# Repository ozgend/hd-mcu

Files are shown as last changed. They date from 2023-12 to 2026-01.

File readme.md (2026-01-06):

# hd-mcu

## bluetooth supported mcu for harley davidson 99-03 with raspberry pi pico

this is not a ecu but a diy -and for fun- project for a monitoring hardware via an mcu since there is no [can-bus](https://en.wikipedia.org/wiki/CAN_bus) support for 99-03 models. it replaces the default turn signal module (tsm) to provide monitoring features for battery voltage, rpm, voes, ignition, and external thermo sensors via bluetooth to the mobile application. it does not involve a reverse engineering for the original hd-tsm module.

- programmable idle timeout for turn signal
- pcb provides signal switching via h-bridge module or mosfet + oc
- built-in battery voltage sensor
- built-in rpm reader
- built-in temperature sensor via rpi-pico
- aux inputs for ignition and voes signals _(may require custom ignition module ie. [ultima/dyna 2000i](./doc/ud2000i.pdf))_
- vehicle information with editable fields for maintenance records
- external 6x thermocpouler raiser for max6670
- supports up to 8x thermocpouler sensors for various purposes

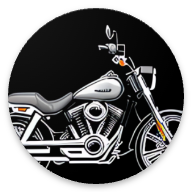
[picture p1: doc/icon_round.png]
icon


### features

- [x] hardware serial
  - [x] raw ft232 usb serial
- [x] bluetooth serial
  - [x] raw bluetooth serial (hc-06 @ 9600 bps)
  - [x] mobile app
- [x] data polling/broadcasting
  - [x] reduced power consumption
  - [x] reduced cpu clock usage
- [x] turn signal flasher module
  - [x] left/right turn signal flasher
  - [x] hazard flasher
  - [x] flash on startup
  - [x] adjustable flash rate
- [x] throttle control module
  - [x] linear hall sensor input
  - [x] servo pwm output
  - [x] adjustable base parameters
  - [x] adjustable idle speed
  - [ ]
  - [ ] adjustable throttle curves
- [x] supported sensor inputs
  - [x] multiplexed thermocouples
    - [x] up to 8 thermocouples
  - [x] direct sensor inputs
    - [x] uptime counter (onboard)
    - [x] mcu voltage (onboard)
    - [x] temperature (onboard)
    - [x] vbus input (onboard)
    - [x] battery voltage input
    - [x] rpm input
    - [x] speed input
  - [ ] tpms
    - [ ] 433mhz receiver implementation
    - [ ] tpms decoder / man-i or man-ii (tbd)
  - [ ] ignition module
    - [ ] dyna 2000i / ultima 2000i timer & pickup
    - [ ] programmable ignition advance
      - [ ] advance curve
      - [ ] temp compensation
      - [ ] rpm compensation
      - [ ] wideband o2 sensor for afr

### software

**mobile app**

- platform

  - `react 18.2.0`
  - `react-native: 0.73.2`

- react-native
  - [x] android
  - [ ] ios

### mobile app ui

back

**mcu firmware**

- platform

  - `nodejs: 20`
  - [`kaluma-cli: 1.4.0`](https://kalumajs.org/docs/getting-started)
  - [`kalumajs runtime: 1.2.1`](https://kalumajs.org/download/)

- FLASH: 2044/24 kb
- SRAM: 264 total, 184/62 kb

### hardware

**assembly**

- 12v-5v buck converter / switching regulator
  - [lm2596 datasheet](./doc/lm2596.pdf)
- raspberry pi pico
  - [pinout](https://pico.pinout.xyz/)
  - [datasheet](./doc/pico-datasheet.pdf)
- hc-06 bluetooth module
  - [datasheet](./doc/hc06.pdf)
- `TSM` / turn signal module
  - _(option-1)_ - with mosfet extension board
    - _pick this if your rectifier is 3 pin and charge flux is 12v-15v_
    - [IRF4905 datasheet](./doc/IRF4905.pdf)
  - _(option-2)_ - l298n h-bridge driver module
    - [datasheet](./doc/l298.pdf)
- `THE` / thermocouple module
  - cd4051 multiplexer
    - [datasheet](./doc/cd4051b.pdf)
  - max6675 thermocouple digitizer
    - [datasheet](./doc/MAX6675.pdf)
    - k-type thermocouple (maximum of 8)
- `TCM` / throttle control module
  - [linear hall sensor / 49e](./doc/49e.pdf)
  - [DS3230MG digital servo](./doc/ds3230.pdf)
- 5v super capacitor
- 5805 voltage regulator
- 33k resistor
- 10k resistor
- 7.5k resistor
- 4.7k resistor
- 1k resistor
- 1n4001 diode

### pcb

**front**
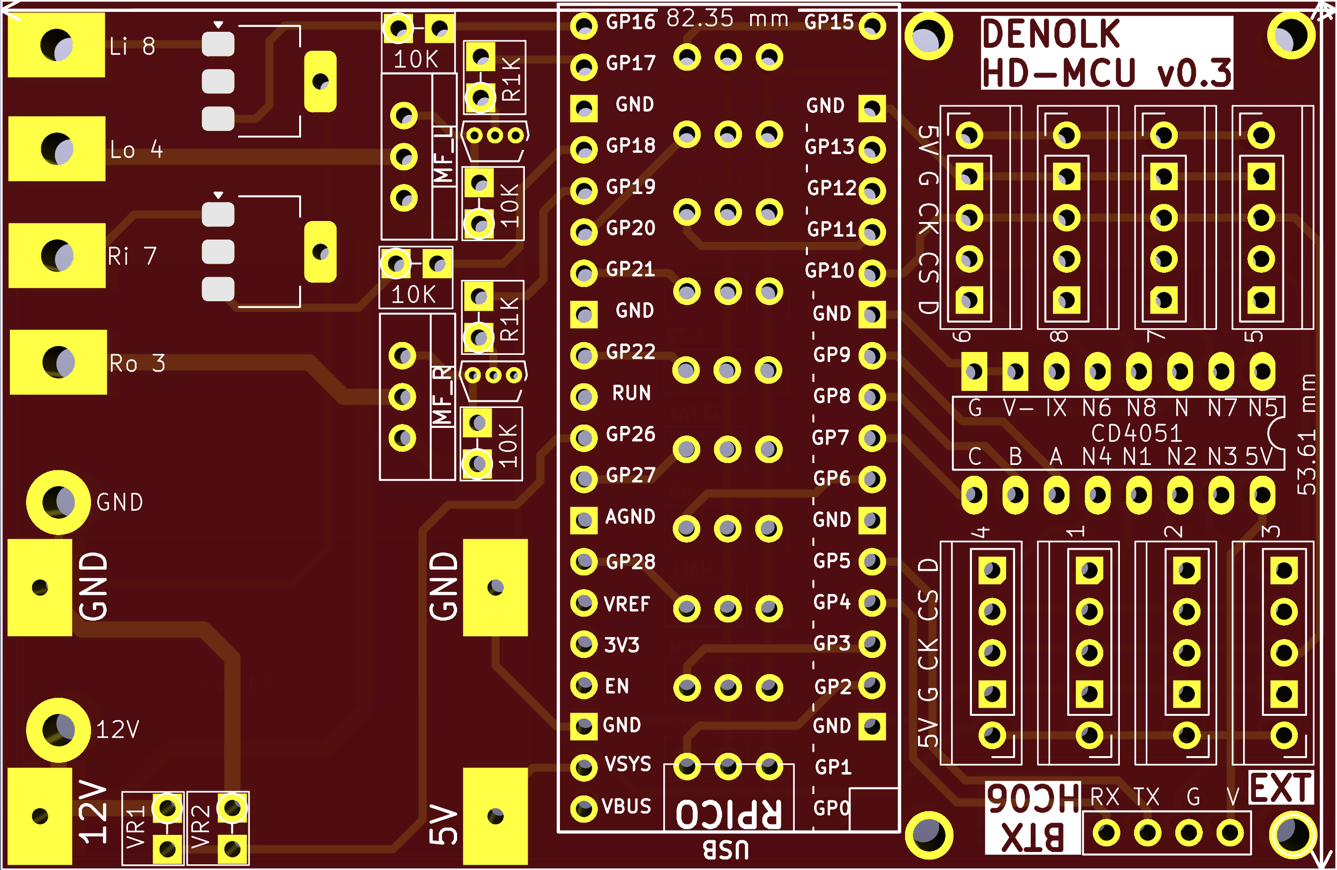
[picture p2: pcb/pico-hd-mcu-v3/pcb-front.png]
front


**back**
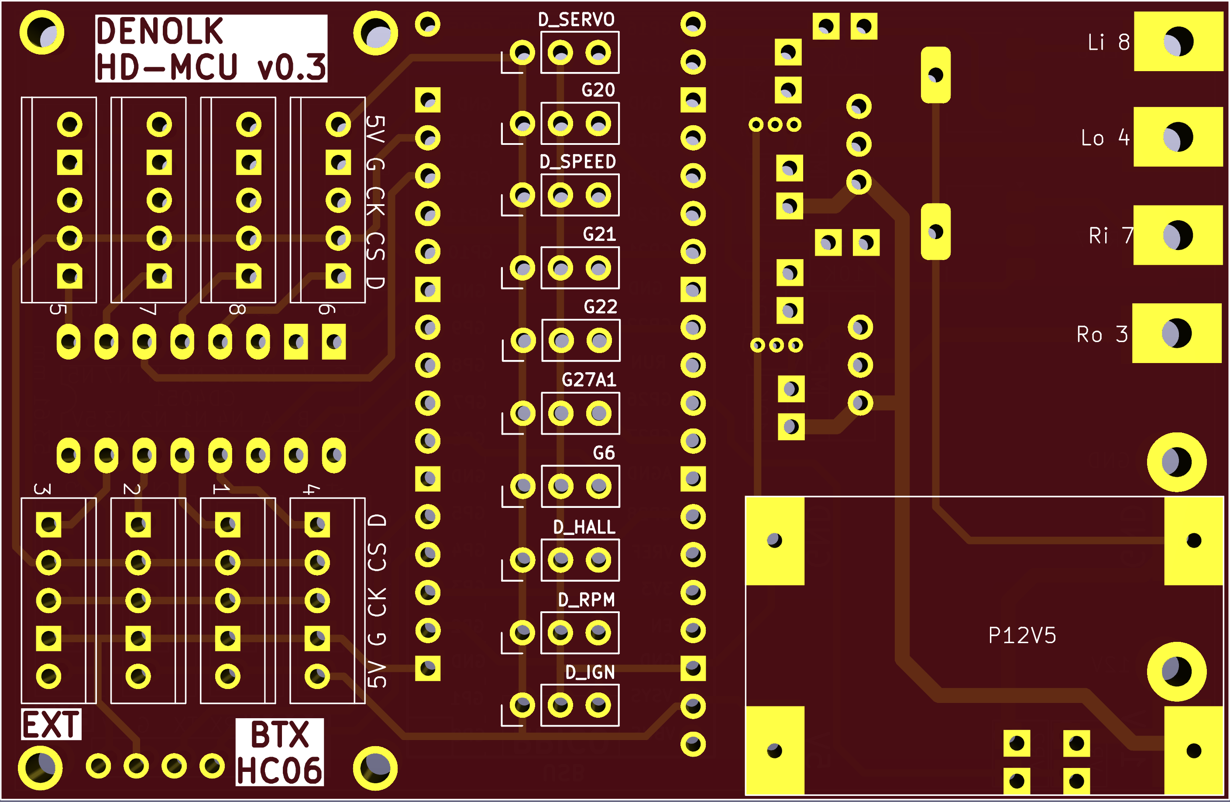
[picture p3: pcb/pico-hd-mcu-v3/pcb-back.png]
back


**blueprint**
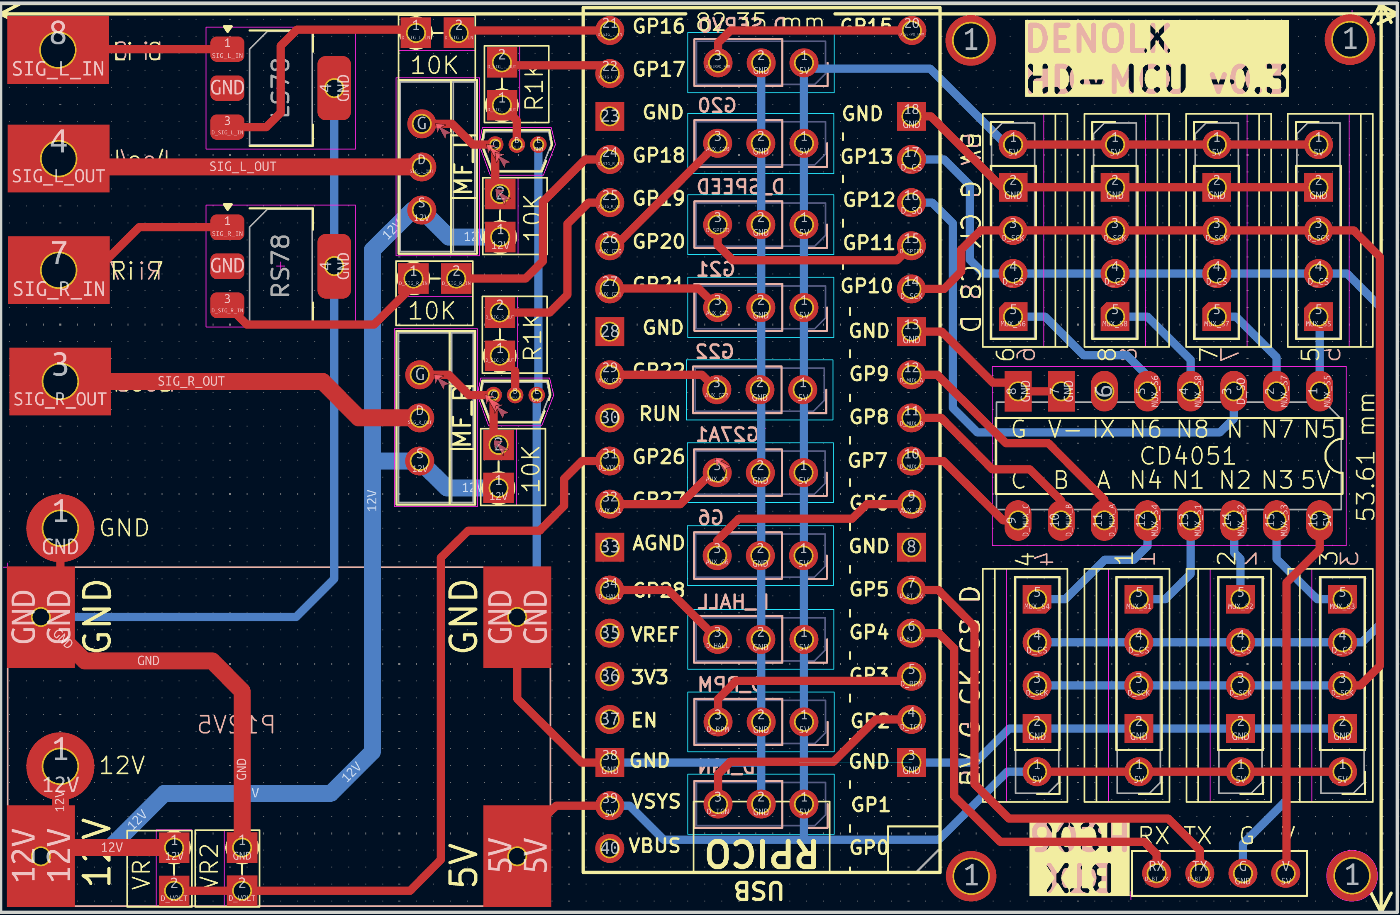
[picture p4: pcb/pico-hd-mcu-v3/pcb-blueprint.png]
raw


### setup & building & installing

- initialization

  ```bash
  git clone
  npm run install
  ```

- cook everything

  ```bash
  npm run build
  ```

- create mcu firmware

  ```bash
  npm build:mcu
  ```

- flash firmware to pico

  ```bash
  npm run flash:mcu -- /dev/tty.usbmodem2XXX
  ```

- create mobile app

  - _create local build_

    ```bash
    npm run build:app
    ```

  - _create distributable bundle .apk_

    ```bash
    nom run bundle:app
    ```

## usb serial interface

- usb: `115200 bps`
- bt: `9600 bps`

### service interaction

- query only: `[SVC]+[CMD]\n`
- set svc data: `[SVC]+[CMD]=[DATA]\n`

**service list:**
| service | description |
| --- | --- |
| `SYS` | mcu information system |
| `THE` | thermocouple sensor module |
| `TSM` | turn signal module |
| `TCM` | throttle control module |
| `VHC` | vehicle healthcheck module |
| `VHI` | vehicle information system |

**command list**
| command | description |
| --- | --- |
| `INFO` | get information from service|
| `DATA` | get data from service |
| `SET` | send data to service |
| `START` | start monitoring |
| `STOP` | stop monitoring |

**`TSM` extended command set**
| command | description |
| --- | --- |
| `LEFT` | left turn signal |
| `RIGHT` | right turn signal |
| `ALL` | hazard signal |
| `NONE` | turn signal off |

### module interaction

- query only: `[MOD]+[CMD]\n`

**module list:**
| name | description |
| --- | --- |
| `M0` | main mcu module |

**command list**
| command | description |
| --- | --- |
| `DIAG` | execute diagnostic |
| `START` | start ON_DEMAND services in module and publish data |
| `STOP` | stop ON_DEMAND services in module and stop publishing data |
| `LIST_ALL` | list all registered services in module |
| `LIST_RUN` | list running/active services in module |

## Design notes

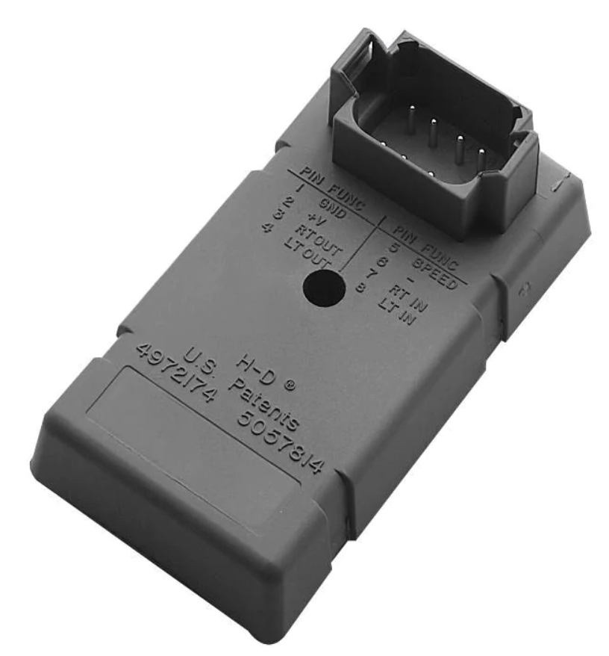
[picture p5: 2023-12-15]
doc/hd-tsm.png

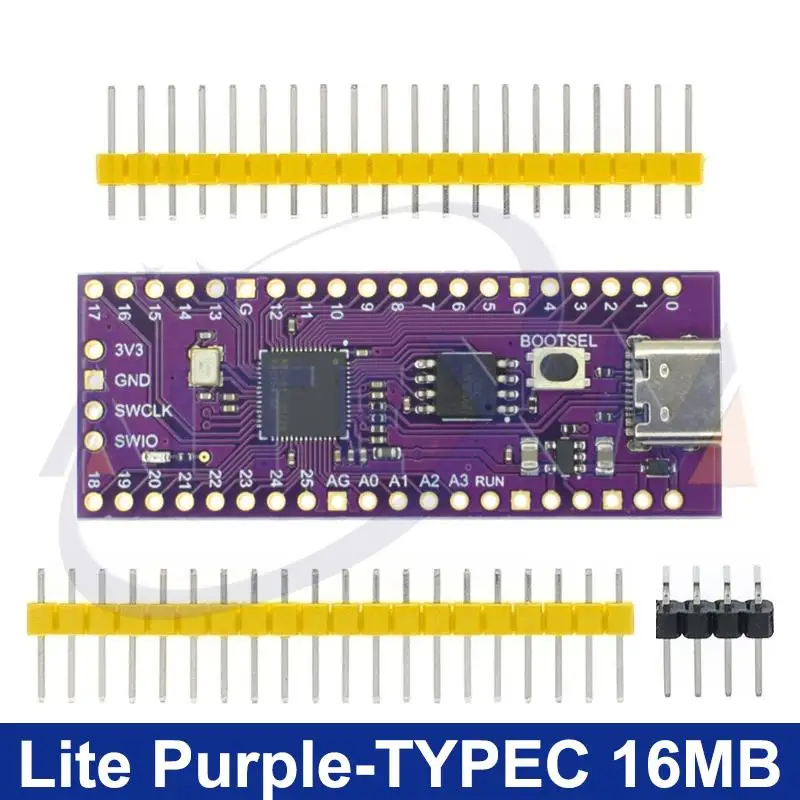
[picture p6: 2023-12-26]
doc/rpi-pico-purple.webp

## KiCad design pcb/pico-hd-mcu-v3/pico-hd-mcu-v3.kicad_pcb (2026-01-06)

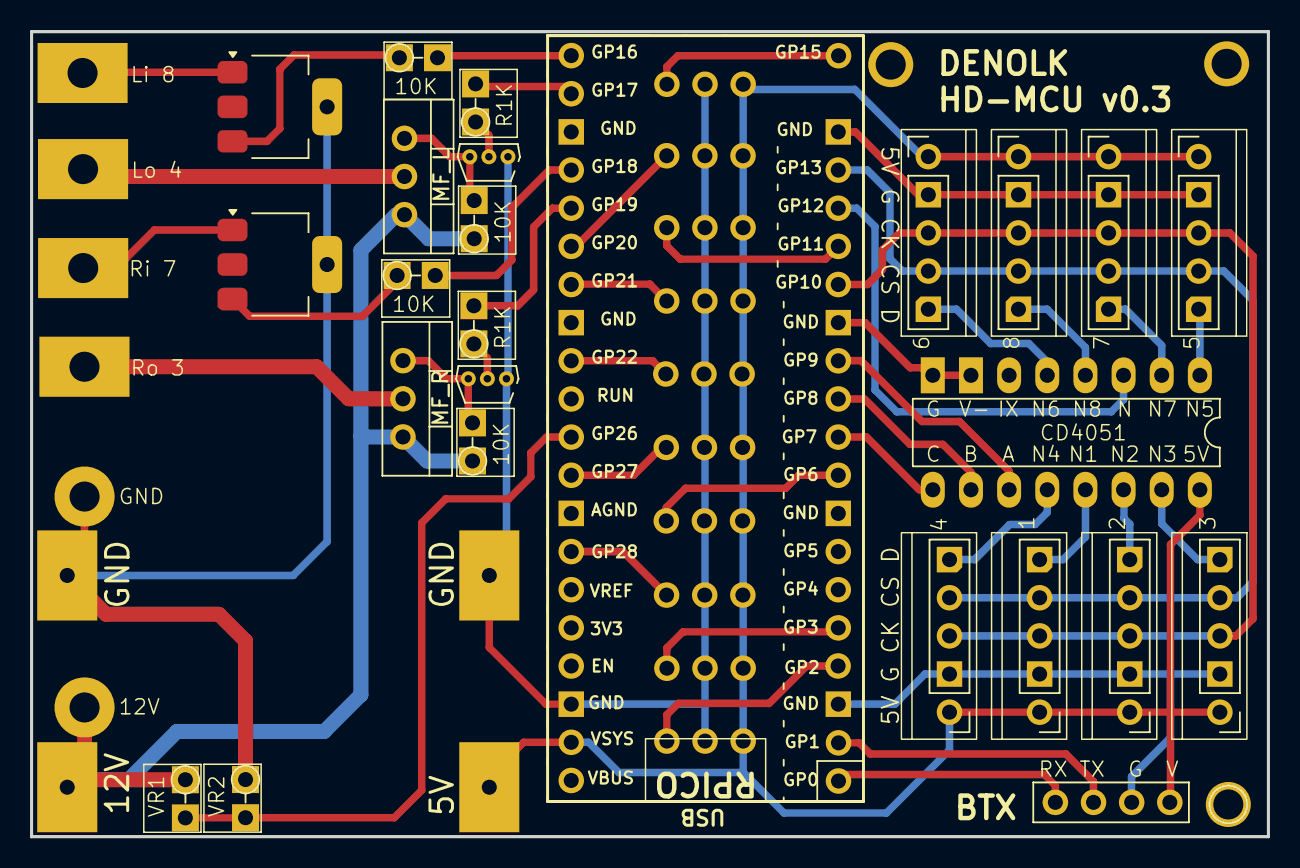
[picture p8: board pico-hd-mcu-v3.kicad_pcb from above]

Board: 2 copper layers, 82.4 x 53.6 mm, 17 parts (0 on the bottom side), 18 nets.

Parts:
1: N1; Socker_PinHeader_1x05_P2.54mm_Dualside
2, 3, 4, 5: N4; Socker_PinHeader_1x05_P2.54mm_Dualside
6: N6; Socker_PinHeader_1x05_P2.54mm_Dualside
7: N7; Socker_PinHeader_1x05_P2.54mm_Dualside
8: N8; Socker_PinHeader_1x05_P2.54mm_Dualside
10K, 10K#2, 10K#3, 10K#4: R_Axial_DIN0204_L3.6mm_D1.6mm_P2.54mm_Vertical
CD4051: CD4051; DIP-16_W7.62mm_LongPads
R1K, R1K#2: R_Axial_DIN0204_L3.6mm_D1.6mm_P2.54mm_Vertical
VR1, VR2: R_Axial_DIN0204_L3.6mm_D1.6mm_P2.54mm_Vertical

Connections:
5V: 1.1, 2.1, 3.1, 4.1, 5.1, 6.1, 7.1, 8.1, CD4051.16
12V: 10K#2.1, 10K#4.1, VR1.1
D_CS: 1.4, 2.4, 3.4, 4.4, 5.4, 6.4, 7.4, 8.4
D_SCK: 1.3, 2.3, 3.3, 4.3, 5.3, 6.3, 7.3, 8.3
D_SIG_L_IN: 10K.1, 10K.2
D_SIG_L_OUT: R1K#2.1, R1K#2.2
D_SIG_R_IN: 10K#3.1, 10K#3.2
D_SIG_R_OUT: R1K.1, R1K.2
D_VOLT: VR1.2, VR2.2
GND: 1.2, 2.2, 3.2, 4.2, 5.2, 6.2, 7.2, 8.2, CD4051.7, CD4051.8, VR2.1
MUX_S1: 1.5, CD4051.13
MUX_S2: 2.5, CD4051.14
MUX_S3: 3.5, CD4051.15
MUX_S4: 4.5, CD4051.12
MUX_S5: 5.5, CD4051.1
MUX_S6: 6.5, CD4051.5
MUX_S7: 7.5, CD4051.2
MUX_S8: 8.5, CD4051.4

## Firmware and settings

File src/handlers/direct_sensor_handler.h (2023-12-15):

#ifndef __direct_sensor_handler__
#define __direct_sensor_handler__

#include "../base_handler.h"
#include <OneWire.h>
#include <DallasTemperature.h>

#define DIRECT_CHANNEL_SIZE 5
#define DIRECT_UPDATE_INTERVAL 1000

#define DIRECT_CHANNEL_UPTIME 0
#define DIRECT_CHANNEL_VOLTAGE 1
#define DIRECT_CHANNEL_TEMPERATURE 2
#define DIRECT_CHANNEL_RPM 3
#define DIRECT_CHANNEL_SPEED 4

#define VOLTAGE_R1 32500.0       // ohm
#define VOLTAGE_R2 7500.0        // ohm
#define SENSOR_ADC_LOSS 0.06     // percent
#define SENSOR_ADC_REFERENCE 3.3 // volts
#define SENSOR_ADC_RESOLUTION 1024.0

class DirectSensorHandler : public BaseHandler
{
public:
  DirectSensorHandler(SerialCom *com) : BaseHandler(F("DirectSensorHandler"), SERVICE_TYPE_DYNAMIC, com)
  {
  }

  void initialize()
  {
    this->_com->writeConsole(F("init.DirectSensorHandler +"));
    pinMode(PIN_SENSOR_VOLTAGE, INPUT);
    pinMode(PIN_SENSOR_TEMP, INPUT);
    pinMode(PIN_SENSOR_RPM, INPUT);
    pinMode(PIN_SENSOR_SPEED, INPUT);
    this->_com->writeConsole(F("init.DirectSensorHandler - done"));
  }

  void update()
  {
    if (!isRunning)
    {
      return;
    }

    if (millis() - _lastUpdateTime < DIRECT_UPDATE_INTERVAL)
    {
      return;
    }

    readAll();
    sendAll();

    _lastUpdateTime = millis();
  }

  void start()
  {
    if (isRunning)
    {
      return;
    }
    this->_com->writeConsole(F("start.DirectSensorHandler +"));
    _oneWire = &OneWire(PIN_SENSOR_TEMP);
    _airTempSensor = &DallasTemperature(_oneWire);
    _airTempSensor->begin();
    this->_com->writeConsole(F("start.DDirectSensorHandler - started"));
    isRunning = true;
  }

  void stop()
  {
    if (!isRunning)
    {
      return;
    }
    this->_com->writeConsole(F("stop.DirectSensorHandler - stopping"));
    delete _airTempSensor;
    delete _oneWire;
    this->_com->writeConsole(F("stop.DirectSensorHandler - stopped"));
    isRunning = false;
  }

private:
  OneWire *_oneWire;
  DallasTemperature *_airTempSensor;
  int _adcValue;
  float _adcVolts;

  long _lastUpdateTime;
  float _sensorValues[DIRECT_CHANNEL_SIZE] = {-1, -1, -1, -1, -1};

  void readVoltage()
  {
    _adcValue = analogRead(PIN_SENSOR_VOLTAGE); // 800-806
    _adcVolts = (_adcValue * SENSOR_ADC_REFERENCE) / SENSOR_ADC_RESOLUTION;
    _adcVolts = _adcVolts - (_adcVolts * SENSOR_ADC_LOSS);
    _sensorValues[DIRECT_CHANNEL_VOLTAGE] = _adcVolts / (VOLTAGE_R2 / (VOLTAGE_R1 + VOLTAGE_R2));
  }

  void readAirTemperature()
  {
    _airTempSensor->requestTemperatures();
    _sensorValues[DIRECT_CHANNEL_TEMPERATURE] = _airTempSensor->getTempCByIndex(0);
  }

  void readRpm()
  {
    _sensorValues[DIRECT_CHANNEL_RPM] = -1;
  }

  void readSpeed()
  {
    _sensorValues[DIRECT_CHANNEL_SPEED] = -1;
  }

  void readAll()
  {
    _sensorValues[DIRECT_CHANNEL_UPTIME] = millis();
    readVoltage();
    readAirTemperature();
    readRpm();
    readSpeed();
  }

  void sendAll()
  {
    for (int i = 0; i < DIRECT_CHANNEL_SIZE; i++)
    {
      sendData(String(F("dts_")) + String(i), String(_sensorValues[i]));
    }
  }
};

#endif

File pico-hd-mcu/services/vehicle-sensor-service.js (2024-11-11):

const logger = require('../logger');
const BaseService = require('../base-service');
const { VehicleSensorData } = require('../../ts-schema/data.model');
const { ServiceCode, Gpio, ServiceType, Hardware, Broadcasting } = require('../../ts-schema/constants');

const BATTERY_VOLTAGE_SCALING_FACTOR = (Hardware.BATTERY_VOLTAGE_R1 + Hardware.BATTERY_VOLTAGE_R2) / Hardware.BATTERY_VOLTAGE_R2;

class VehicleSensorService extends BaseService {
  rpmSignalCounter = 0;
  rpmSignalLastTime = 0;

  constructor(eventBus) {
    super(eventBus, {
      serviceCode: ServiceCode.VehicleSensor,
      serviceType: ServiceType.ON_DEMAND,
      broadcastMode: Broadcasting.OnDemandPolling,
    });
    this.data = new VehicleSensorData();
  }

  start() {
    super.start();
    attachInterrupt(Gpio.VEHICLE_SENSOR_RPM, this.interruptRpmHandler, RISING);
  }

  stop() {
    super.stop();
    detachInterrupt(Gpio.VEHICLE_SENSOR_RPM);
  }

  interruptRpmHandler() {
    this.rpmSignalCounter++;
    console.log('rpm signal counter', this.rpmSignalCounter);
  }

  calculateRpm() {
    // todo: implement with harley davidson rpm sensor output voltage reference
    // const rawRpm = analogRead(Gpio.VEHICLE_SENSOR_RPM);
    // this.data.raw_rpm = rawRpm;
    // this.data.rpm = rawRpm;
    this.data.rpm = -1;

    const currentTime = millis();
    const deltaTime = currentTime - this.rpmSignalLastTime;

    if (deltaTime > 0) {
      this.data.rpm = this.rpmSignalCounter / deltaTime * 1000 * 60;
    }

    this.rpmSignalCounter = 0;
    this.rpmSignalLastTime = currentTime;
  }

  calculateSpeed() {
    // todo: implement with harley davidson speed sensor output voltage reference
    // const rawSpeed = analogRead(Gpio.VEHICLE_SENSOR_SPEED);
    // this.data.raw_speed = rawSpeed;
    // this.data.speed = rawSpeed;
    this.data.speed = -1;
  }

  calculateTpmsData() {
    // todo: implement with tpms sensor output
    this.data.tireFront = -1;
    this.data.tireRear = -1;
    this.data.tempFront = -1;
    this.data.tempRear = -1;
  }

  calculateTemperature() {
    this.data.raw_temp = analogRead(Gpio.VEHICLE_SENSOR_TEMP);
    this.data.raw_temp_volts = this.data.raw_temp * Hardware.ADC_REF_MAX_VOLTAGE;
    this.data.temp = Hardware.TEMPERATURE_OFFSET - (this.data.raw_temp_volts - Hardware.ADC_OFFSET_VOLTAGE) / Hardware.TEMPERATURE_SCALING_FACTOR;
  }

  calculateVref() {
    this.data.raw_vref = analogRead(Gpio.VEHICLE_SENSOR_VREF);
    this.data.vref = this.data.raw_vref * Hardware.ADC_SCALING_FACTOR;
  }

  calculateBattery() {
    this.data.raw_batt = analogRead(Gpio.VEHICLE_SENSOR_BATT);
    this.data.batt = this.data.raw_batt * Hardware.ADC_REF_MAX_VOLTAGE * BATTERY_VOLTAGE_SCALING_FACTOR;
  }

  setup() {
    super.setup();
    // pinMode(Gpio.VEHICLE_SENSOR_VREF, INPUT);
    // pinMode(Gpio.VEHICLE_SENSOR_TEMP, INPUT);
    pinMode(Gpio.VEHICLE_SENSOR_BATT, INPUT);
    pinMode(Gpio.VEHICLE_SENSOR_AUX, INPUT);
    pinMode(Gpio.VEHICLE_SENSOR_RPM, INPUT);
    pinMode(Gpio.VEHICLE_SENSOR_SPEED, INPUT);
    pinMode(Gpio.VEHICLE_SENSOR_IGN, INPUT);
  }

  publishData() {
    this.data.uptime = millis();

    this.calculateTemperature();
    this.calculateVref();
    this.calculateBattery();
    this.calculateRpm();
    this.calculateSpeed();
    this.calculateTpmsData();

    super.publishData();
  }


};

module.exports = VehicleSensorService;

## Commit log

2023-12-14 refactoring (#1)
    * optimize memory usage 1700b to 570b
    * optimize pin assignments
    * remove pin map
2023-12-15 pcb unified (#2)
    * hw pin update
    * update pinout
    * add pcb blueprint
    * update readme
    * refactor Ax sensor pin layout
    * pcb routing optimize
    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
    [hd-mcu-v2.kicad_pcb]
2023-12-15 add serial commands
    [hd-mcu-v2.kicad_pcb]
2023-12-15 switch to index based keys
2023-12-15 serial commands (#4)
    * add serial commands
    * fix peripheral alloc
    * serialize json & stream at once per service
    * switch to index based keys
    * remote tsm
    [hd-mcu-v2.kicad_pcb]
2023-12-16 update pcb
    [hd-mcu-v2.kicad_pcb]
2023-12-19 Serial commands (#5)
    * update pcb
    * update bt serial
    * fix serial com sw
    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
    [hd-mcu-v2.kicad_pcb]
2023-12-19 wip pcb
    [hd-mcu-v2.kicad_pcb]
2023-12-21 wip - pico port nodejs
2023-12-22 ref pin
2023-12-22 fix uart data rx
2023-12-25 add muxed sensor service
2023-12-25 reset timer clock rtc
2023-12-25 spi hw/sw
2023-12-25 pico purple board pinout
2023-12-25 tsm interrupt wip
2023-12-26 add ref docs
    [hd-mcu-v2.kicad_pcb, nano-hd-mcu-v2.kicad_pcb, pico-hd-mcu-v2.kicad_pcb]
2024-01-04 calculate dev adc sensors
2024-01-09 update mcu according to pico gpio
    [pico-hd-mcu-v2.kicad_pcb]
2024-01-09 update voltage divider
2024-01-18 refactor to work with polled device data and info
2024-01-18 add bt device discovery
2024-01-19 add device discovery for bonded devices only
2024-01-23 more sensor values & info edit
2024-02-07 pcb update
    [pico-hd-mcu-v2.kicad_pcb]
2024-04-30 drop arduino nano support
    [nano-hd-mcu-v2.kicad_pcb]
2024-05-01 add pcb plots
    [pico-hd-mcu-v2-B_Cu.gbl, pico-hd-mcu-v2-B_Mask.gbs, pico-hd-mcu-v2-B_Paste.gbp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]
2024-05-01 updatee vehicle info props
2024-05-07 added 12v5 power supply submodule
    [pico-hd-mcu-v2-B_Cu.gbl, pico-hd-mcu-v2-B_Mask.gbs, pico-hd-mcu-v2-B_Paste.gbp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]
2024-05-07 update plots
    [pico-hd-mcu-v2-B_Cu.gbl, pico-hd-mcu-v2-B_Mask.gbs, pico-hd-mcu-v2-B_Paste.gbp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]
2024-05-07 updat pcb add drill holes
    [pico-hd-mcu-v2-B_Cu.gbl, pico-hd-mcu-v2-B_Mask.gbs, pico-hd-mcu-v2-B_Paste.gbp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]
2024-05-09 add extension board for mux x4
    [pico-hd-mcu-v2-B_Cu.gbl, pico-hd-mcu-v2-B_Mask.gbs, pico-hd-mcu-v2-B_Paste.gbp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]
2024-05-09 pcb fix drc exclusion
2024-05-20 update pcb - ext mosfet switch
    [pico-hd-mcu-v2-B_Cu.gbl, pico-hd-mcu-v2-B_Mask.gbs, pico-hd-mcu-v2-B_Paste.gbp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]
2024-05-21 fix vhc adc temp sensor
    [vehicle-sensor-service.js]
2024-05-28 update plot
    [pico-hd-mcu-v2-B_Cu.gbl, pico-hd-mcu-v2-B_Mask.gbs, pico-hd-mcu-v2-B_Paste.gbp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]
2024-05-29 onboard led
2024-05-29 fix spi handler
2024-10-30 fix adc vref and adc0 reading + scaling
    [vehicle-sensor-service.js]
2024-11-08 toggle onboard led for diag
2024-11-11 adjust tsm interrupts & timing
2024-11-11 extend rw tsm interrupt and timing config
2024-11-11 add tsm interrupt button as input_pullup
2025-05-29 pin assignment for ign module
2025-10-01 fix adc reading
2025-10-01 init pcbv3
    [pico-hd-mcu-v3.kicad_pcb]
2025-12-29 fix runtime services and temperature reading
2025-12-29 add throttle controller
2025-12-29 update throttle servo controller
2025-12-30 pcbv3 stub
    [pico-hd-mcu-v3.kicad_pcb]
2026-01-05 refactor - adc hall sensor
2026-01-06 mcu - improve throttle controller
2026-01-06 app - throttle control data view
2026-01-06 pcb - v3 wip
    [pico-hd-mcu-v3.kicad_pcb]
2026-01-06 hardware gpio remapping
    [pico-hd-mcu-v3.kicad_pcb]
2026-01-06 update pcb v3
    [pico-hd-mcu-v3-B_Cu.gbl, pico-hd-mcu-v3-B_Mask.gbs, pico-hd-mcu-v3-B_Paste.gbp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]
2026-01-06 fallback to uart0 for bt rx/tx
    [pico-hd-mcu-v3-B_Cu.gbl, pico-hd-mcu-v3-B_Mask.gbs, pico-hd-mcu-v3-B_Paste.gbp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]
